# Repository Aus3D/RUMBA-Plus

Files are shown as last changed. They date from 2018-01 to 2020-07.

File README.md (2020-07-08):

# RUMBA+




RUMBA+ is an updated version of the RUMBA 3D Printer control board, originally developed by [RepRapDiscount](http://www.reprapdiscount.com/). 

The RUMBA+ update is designed to address several shortcomings with the original design, and improve on the otherwise solid framework it presents. More information on RUMBA is available on the RepRapWiki page [here](http://reprap.org/wiki/RUMBA).

Some of the key improvements in the RUMBA+ design include:
* Full 12/24V Compatibility (original RUMBA had 16V limit on bed)
* Better, logic-level MOSFETs which generate less heat (can handle higher currents + safer & more reliable)
* Improved power supply circuitry, including:
  * 5V and 12V regulators completely overhauled for higher current + less heat
  * Automatic power-select between USB or 12/24V
* Higher quality screw terminals for power input / heated bed (higher current rating + easier to work with heavy-gauge wire)
* Dozens of smaller changes to improve reliability or performance - refer to the [release page](https://github.com/Aus3D/RUMBA-Plus/releases) for a detailed change history.

RUMBA+ boards are for sale in the [Aus3D shop](http://aus3d.com.au/rumba-plus). Additional documentation is available on the [Aus3D wiki](http://wiki.aus3d.com.au/RUMBA_Plus).

In keeping with the original RUMBA design, RUMBA+ is fully open source.

## Images
### Overview
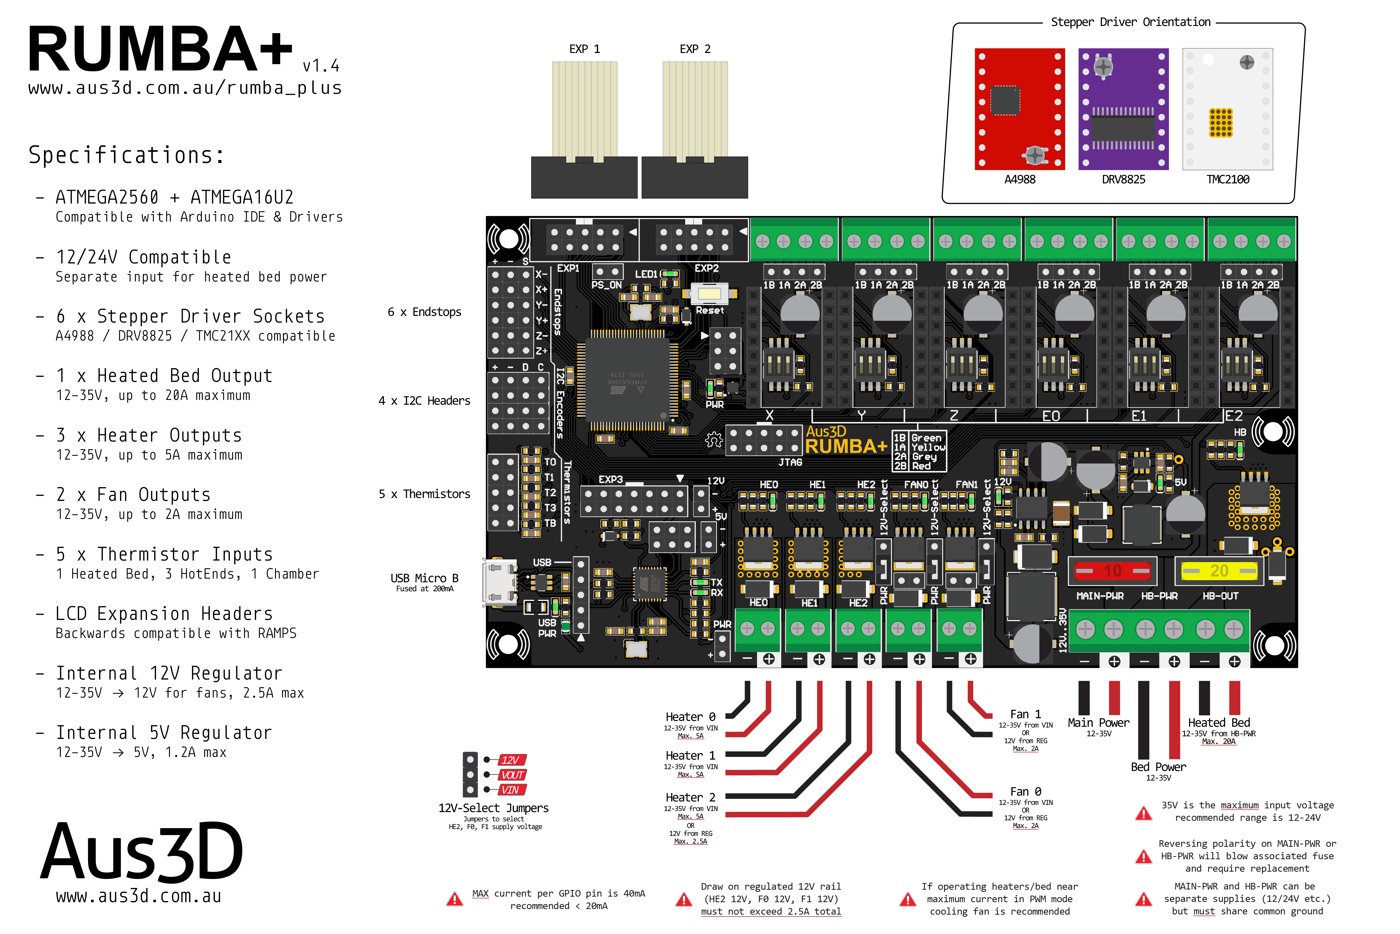
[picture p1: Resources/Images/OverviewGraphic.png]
RUMBA+ Overview

### Photo
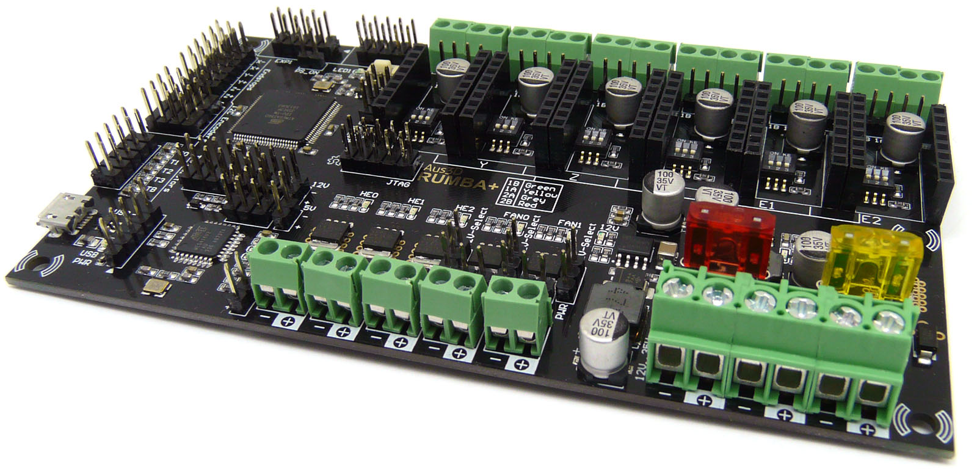
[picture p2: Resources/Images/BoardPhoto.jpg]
RUMBA+ Photo

### Schematic
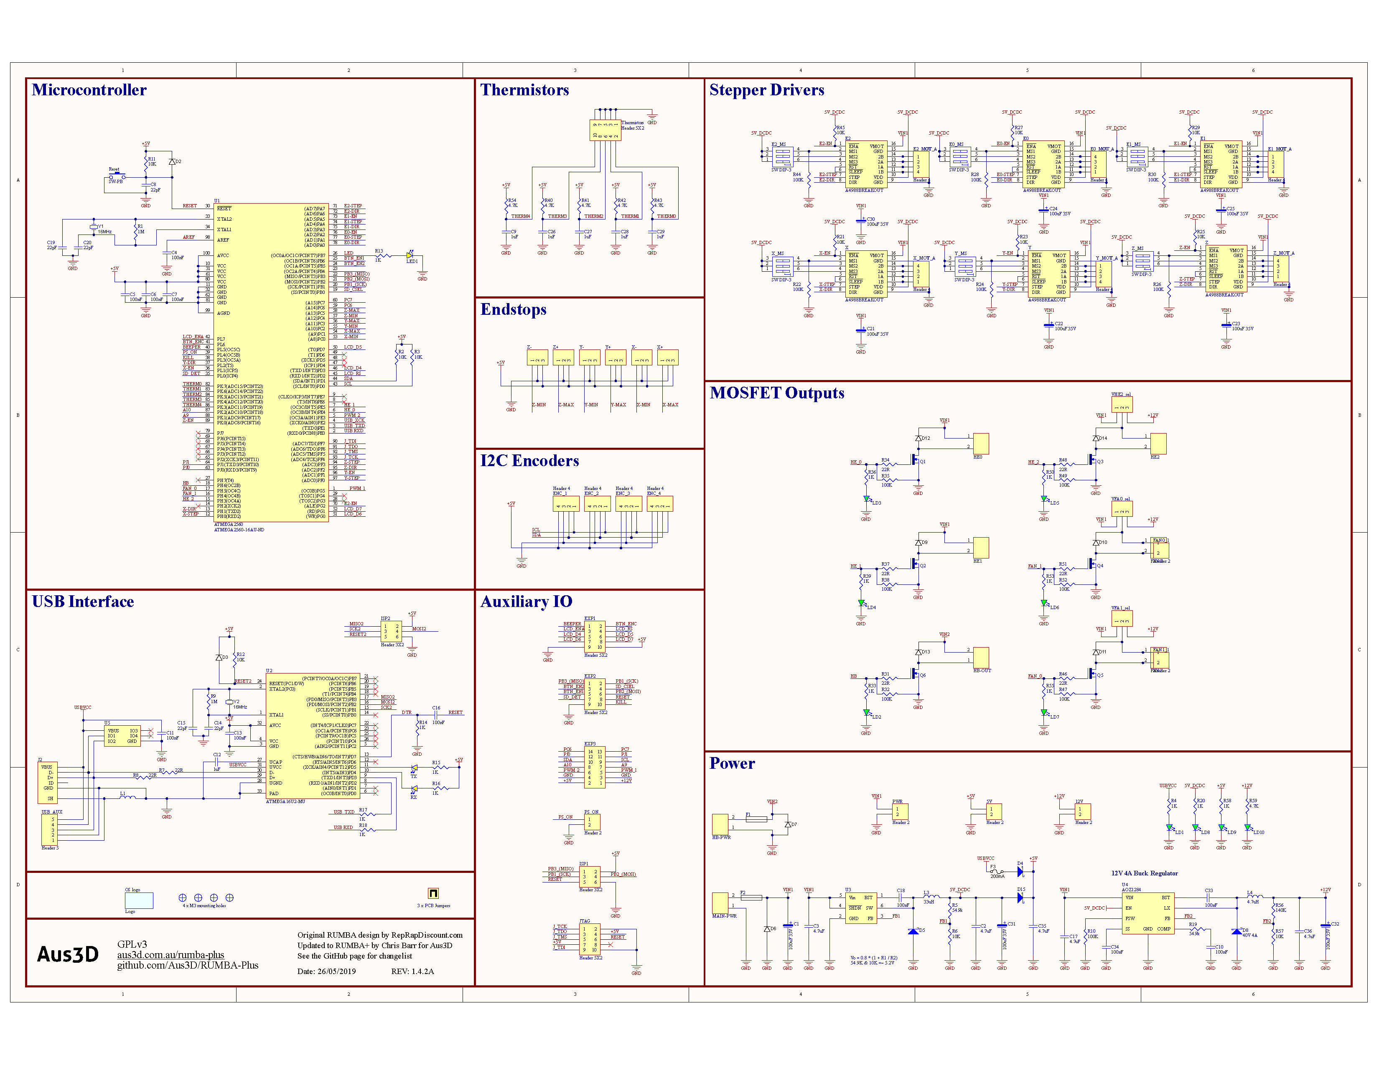
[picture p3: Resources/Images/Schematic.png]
RUMBA+ Schematic

### Pinout
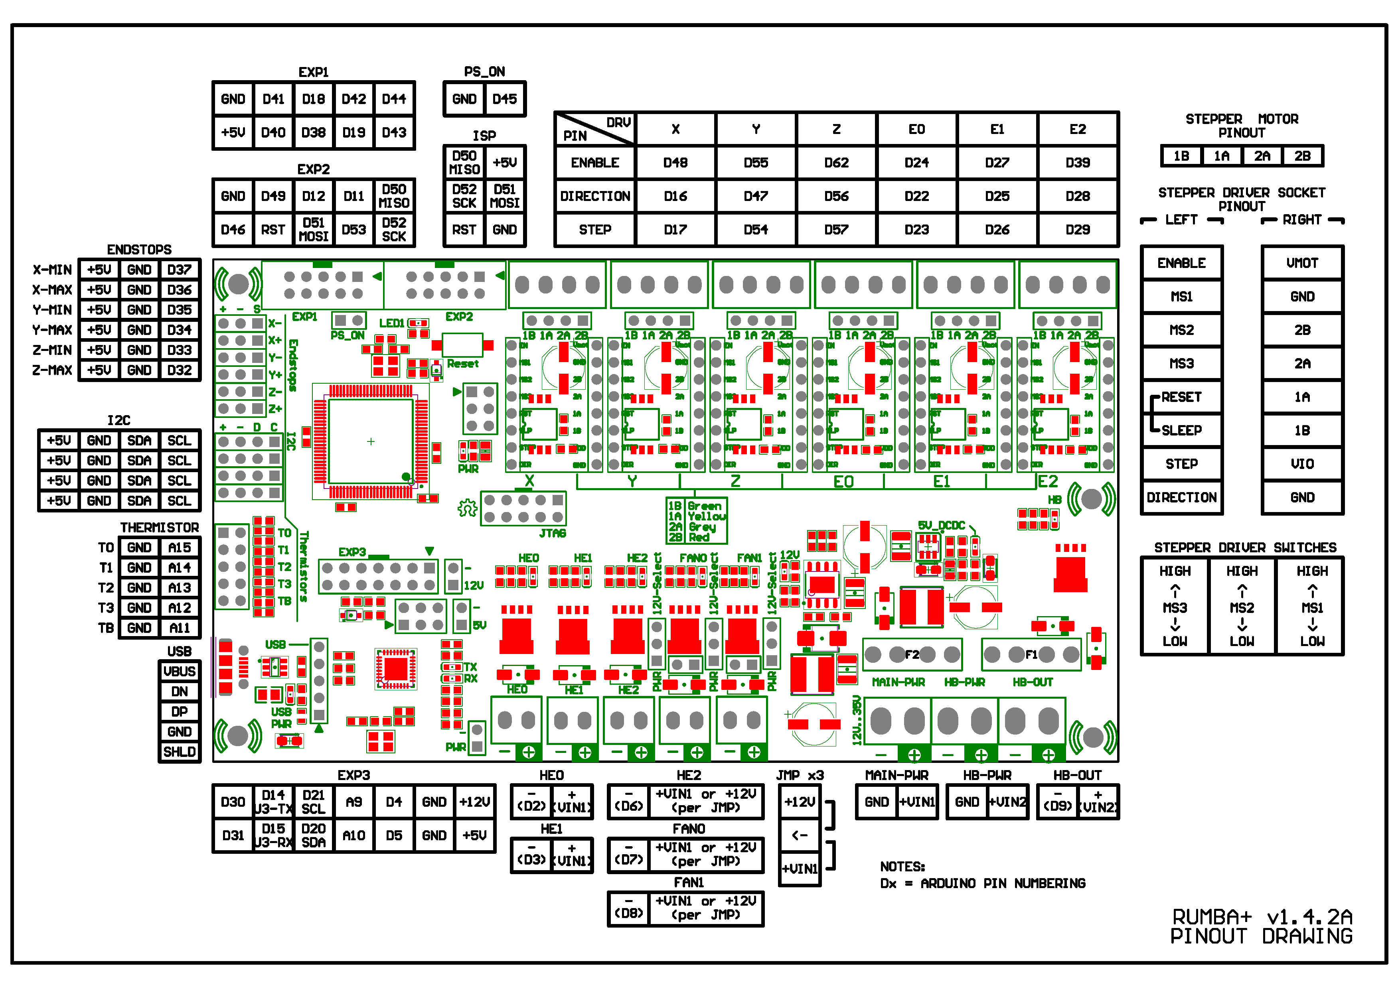
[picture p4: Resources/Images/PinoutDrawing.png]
RUMBA+ Pinout

### Dimensions
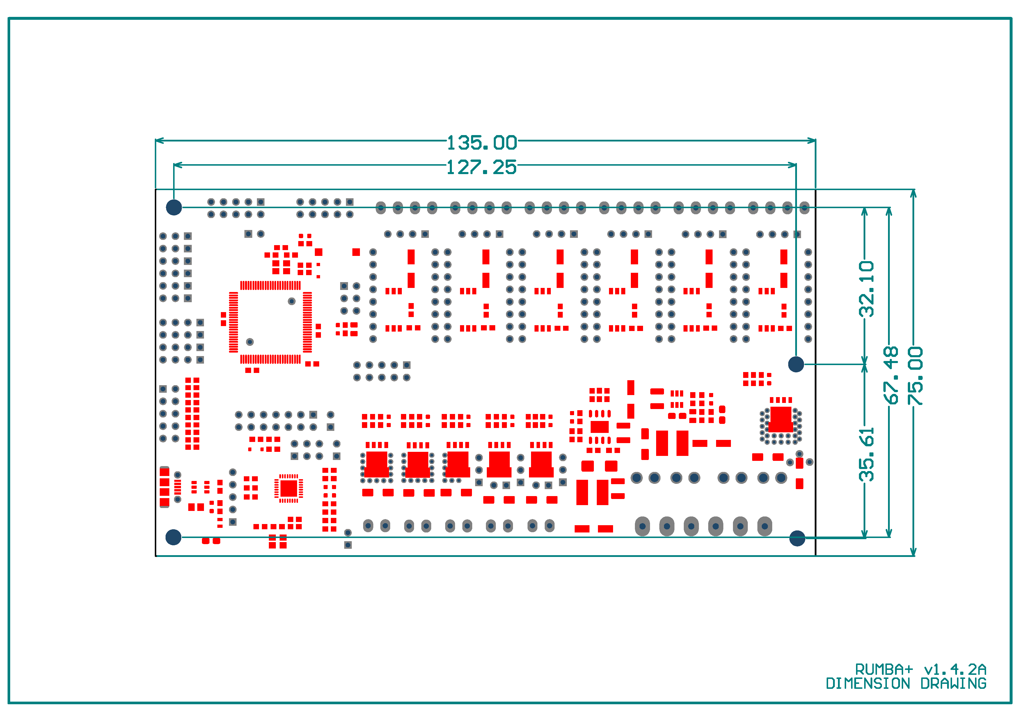
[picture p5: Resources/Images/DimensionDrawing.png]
RUMBA+ Dimensions


## License
RUMBA+ is fully open source, and may be freely modified or changed by anyone, provided they maintain the license it is released under. The design is free to use for any purpose, including commercial uses. RUMBA+ maintains the GPLv2 license of the original RUMBA board. For more information on this license, please see the included license file.

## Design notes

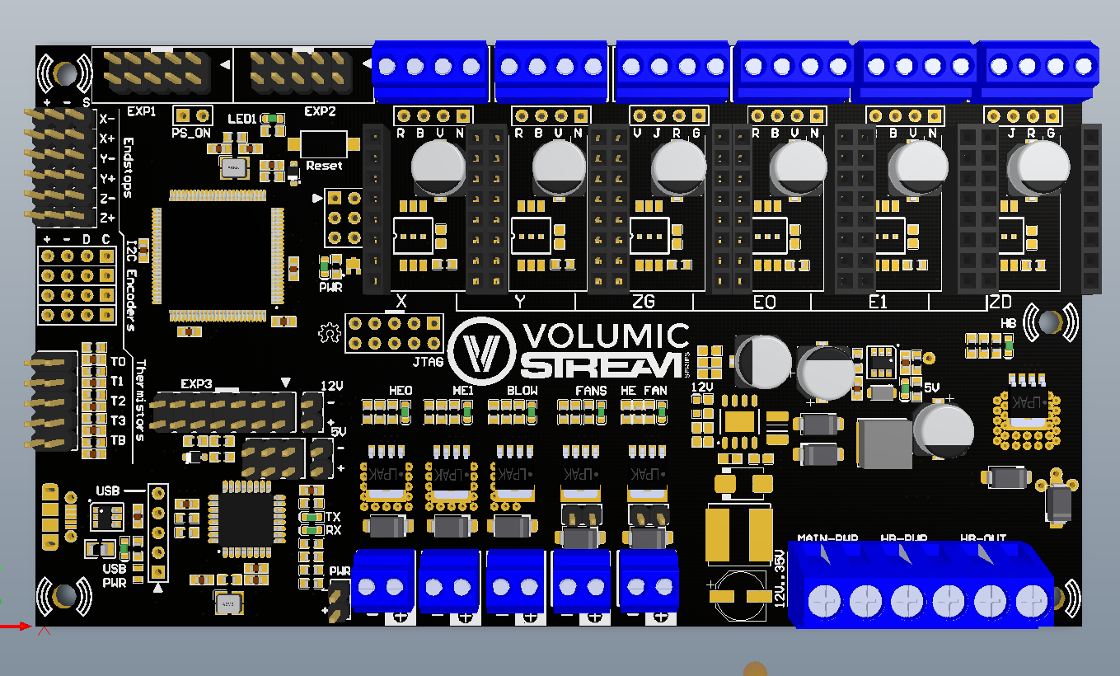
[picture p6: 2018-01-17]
V3D-RUMBA_plus_BoardPreviewTop_1_4_0.png

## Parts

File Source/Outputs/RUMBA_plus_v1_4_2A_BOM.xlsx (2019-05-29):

Designator | Description | Quantity | Note | Manufacturer 1 | Manufacturer Part Number 1 | Supplier 1 | Supplier Part Number 1
JMP | 2.54mm .1" PCB Jumper, Green | 3 | Installed as per drawing, approved sub OK | Sullins (https://octopart-clicks.com/click/altium?sku=S9337-ND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) | QPC02SXGN-RC (https://octopart-clicks.com/click/altium?sku=S9337-ND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) | Digi-Key | S9337-ND (https://octopart-clicks.com/click/altium?sku=S9337-ND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)
C1, C21, C22, C23, C24, C25, C30, C31, C32 | CAP ALUM 100UF 20% 35V SMD | 9 | Approved sub OK | Panasonic (https://octopart-clicks.com/click/altium?sku=PCE5016CT-ND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) | EEEFT1V101AP (https://octopart-clicks.com/click/altium?sku=PCE5016CT-ND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) | Digi-Key | PCE5016CT-ND (https://octopart-clicks.com/click/altium?sku=PCE5016CT-ND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)
C4, C5, C6, C7, C10, C11, C13, C16, C18, C33, C34 | CAP CER 0.1UF 50V X7R 0603 | 11 | Approved sub OK | Yageo (https://octopart-clicks.com/click/altium?sku=311-1344-1-ND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) | CC0603KRX7R9BB104 (https://octopart-clicks.com/click/altium?sku=311-1344-1-ND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) | Digi-Key | 311-1344-1-ND (https://octopart-clicks.com/click/altium?sku=311-1344-1-ND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)
C9, C12, C26, C27, C28, C29 | CAP CER 1UF 16V X7R 0603 | 6 | Approved sub OK | Taiyo Yuden (https://octopart-clicks.com/click/altium?sku=587-1241-1-ND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) | EMK107B7105KA-T (https://octopart-clicks.com/click/altium?sku=587-1241-1-ND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) | Digi-Key | 587-1241-1-ND (https://octopart-clicks.com/click/altium?sku=587-1241-1-ND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)
C2, C35 | CAP CER 4.7UF 10V X7R 0805 | 2 | Approved sub OK | TDK (https://octopart-clicks.com/click/altium?sku=445-14527-1-ND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) | C2012X7R1A475K085AC (https://octopart-clicks.com/click/altium?sku=445-14527-1-ND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) | Digi-Key | 445-14527-1-ND (https://octopart-clicks.com/click/altium?sku=445-14527-1-ND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)
C3, C17, C36 | CAP CER 4.7UF 50V X7R 1210 | 3 | Approved sub OK | KEMET (https://octopart-clicks.com/click/altium?sku=399-6785-1-ND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) | C1210C475K5RACTU (https://octopart-clicks.com/click/altium?sku=399-6785-1-ND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) | Digi-Key | 399-6785-1-ND (https://octopart-clicks.com/click/altium?sku=399-6785-1-ND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)
C8, C14, C15, C19, C20 | CAP CER 22PF 50V X7R 0603 | 5 | Approved sub OK | Kyocera AVX (https://octopart-clicks.com/click/altium?sku=478-6204-1-ND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) | 06035C220JAT2A (https://octopart-clicks.com/click/altium?sku=478-6204-1-ND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) | Digi-Key | 478-6204-1-ND (https://octopart-clicks.com/click/altium?sku=478-6204-1-ND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)
J2 | CONN RCPT USB2.0 MICRO B SMD R/A | 1 | Approved sub OK | Molex (https://octopart-clicks.com/click/altium?sku=WM1399CT-ND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) | 105017-0001 (https://octopart-clicks.com/click/altium?sku=WM1399CT-ND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) | Digi-Key | WM1399CT-ND (https://octopart-clicks.com/click/altium?sku=WM1399CT-ND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)
Y1, Y2 | CRYSTAL 16.0000MHZ 18PF SMD | 2 | Approved sub OK | Epson (https://octopart-clicks.com/click/altium?sku=SER3686CT-ND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) | FA-23816.0000MBC3 (https://octopart-clicks.com/click/altium?sku=SER3686CT-ND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) | Digi-Key | SER3686CT-ND (https://octopart-clicks.com/click/altium?sku=SER3686CT-ND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)
D2, D3 | DIODE GEN PURP 75V 150MA SOD323 | 2 | Approved sub OK | MCC (https://octopart-clicks.com/click/altium?sku=1N4148WXTPMSCT-ND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) | 1N4148WX-TP (https://octopart-clicks.com/click/altium?sku=1N4148WXTPMSCT-ND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) | Digi-Key | 1N4148WXTPMSCT-ND (https://octopart-clicks.com/click/altium?sku=1N4148WXTPMSCT-ND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)
D6, D7, D9, D10, D11, D12, D13, D14 | DIODE GEN PURP 100V 1.5A SMA | 8 | Approved sub OK | Diodes (https://octopart-clicks.com/click/altium?sku=S2BA-FDICT-ND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) | S2BA-13-F (https://octopart-clicks.com/click/altium?sku=S2BA-FDICT-ND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) | Digi-Key | S2BA-FDICT-ND (https://octopart-clicks.com/click/altium?sku=S2BA-FDICT-ND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)
D4, D5, D15 | DIODE SCHOTTKY 40V 2A SOD123F | 3 | Approved sub OK | ON Semiconductor / Fairchild (https://octopart-clicks.com/click/altium?manufacturer=ON%20Semiconductor%20%2F%20Fairchild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) | SS24FL (https://octopart-clicks.com/click/altium?manufacturer=ON%20Semiconductor%20%2F%20Fairchild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) | Digi-Key | SS24FLCT-ND (https://octopart-clicks.com/click/altium?manufacturer=ON%20Semiconductor%20%2F%20Fairchild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)
D8 | DIODE SCHOTTKY 40V 4A DO214AA | 1 | Approved sub OK | General Instruments (https://octopart-clicks.com/click/altium?manufacturer=General%20Instruments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) | SSB44-E3/52T (https://octopart-clicks.com/click/altium?manufacturer=General%20Instruments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) | Digi-Key | SSB44-E3/52TGICT-ND (https://octopart-clicks.com/click/altium?manufacturer=General%20Instruments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)
L1 | FERRITE BEAD 220 OHM 0805 1LN | 1 | Approved sub OK | Murata (https://octopart-clicks.com/click/altium?sku=490-1054-1-ND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) | BLM21PG221SN1D (https://octopart-clicks.com/click/altium?sku=490-1054-1-ND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) | Digi-Key | 490-1054-1-ND (https://octopart-clicks.com/click/altium?sku=490-1054-1-ND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)
L4 | FIXED IND 4.7UH 4.5A 26 MOHM SMD | 1 | Approved sub OK | Bourns (https://octopart-clicks.com/click/altium?sku=SRN6045TA-4R7MCT-ND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) | SRN6045TA-4R7M (https://octopart-clicks.com/click/altium?sku=SRN6045TA-4R7MCT-ND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) | Digi-Key | SRN6045TA-4R7MCT-ND (https://octopart-clicks.com/click/altium?sku=SRN6045TA-4R7MCT-ND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)
L3 | FIXED IND 33UH 1.8A 145 MOHM SMD | 1 | Approved sub OK | Bourns (https://octopart-clicks.com/click/altium?sku=SRN6045TA-330MCT-ND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) | SRN6045TA-330M (https://octopart-clicks.com/click/altium?sku=SRN6045TA-330MCT-ND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) | Digi-Key | SRN6045TA-330MCT-ND (https://octopart-clicks.com/click/altium?sku=SRN6045TA-330MCT-ND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)
F1, F2 | FUSE HOLDER BLADE PCB | 2 | Approved sub OK | Memory Protection Devices (https://octopart-clicks.com/click/altium?sku=BK-6013-ND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) | BK-6013 (https://octopart-clicks.com/click/altium?sku=BK-6013-ND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) | Digi-Key | BK-6013-ND (https://octopart-clicks.com/click/altium?sku=BK-6013-ND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)
5V, 12V, FAN0_1, FAN1_1, PS_ON, PWR | Header, 2-Pin | 6 | Approved sub OK | Generic Header
VFA0_sel, VFA1_sel, VHE2_sel, X-, X+, Y-, Y+, Z-, Z+ | Header, 3-Pin | 9 | Approved sub OK | Generic Header
ISP1, ISP2 | Header, 3-Pin, Dual row | 2 | Approved sub OK | Generic Header
E0_MOT_A, E1_MOT_A, E2_MOT_A, ENC_1, ENC_2, ENC_3, ENC_4, X_MOT_A, Y_MOT_A, Z_MOT_A | Header, 4-Pin | 10 | Approved sub OK | Generic Header
USB_AUX | Header, 5-Pin | 1 | Approved sub OK | Generic Header
EXP1, EXP2, JTAG, Thermistors | Header, 5-Pin, Dual row | 4 | Approved sub OK | Generic Header
EXP3 | Header, 7-Pin, Dual row | 1 | Approved sub OK | Generic Header
E0_0, E0_1, E1_0, E1_1, E2_0, E2_1, X_1, X_2, Y_0, Y_1, Z_0, Z_1 | Header, 8-Pin, Female | 12 | Approved sub OK | Generic Header
U2 | IC MCU 8BIT 16KB FLASH 32VQFN | 1 |  | Microchip (https://octopart-clicks.com/click/altium?sku=ATMEGA16U2-MU-ND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) | ATMEGA16U2-MU (https://octopart-clicks.com/click/altium?sku=ATMEGA16U2-MU-ND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) | Digi-Key | ATMEGA16U2-MU-ND (https://octopart-clicks.com/click/altium?sku=ATMEGA16U2-MU-ND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)
U1 | IC MCU 8BIT 256KB FLASH 100TQFP | 1 |  | Microchip / Atmel (https://octopart-clicks.com/click/altium?manufacturer=Microchip%20%2F%20Atmel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) | ATMEGA2560-16AU (https://octopart-clicks.com/click/altium?manufacturer=Microchip%20%2F%20Atmel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) | Digi-Key | ATMEGA2560-16AU-ND (https://octopart-clicks.com/click/altium?manufacturer=Microchip%20%2F%20Atmel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)
U3 | IC REG BUCK ADJ 1.2A SOT23-6 | 1 |  | Alpha & Omega Semiconductor (https://octopart-clicks.com/click/altium?manufacturer=Alpha%20%26%20Omega%20Semiconductor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) | AOZ1282CI (https://octopart-clicks.com/click/altium?manufacturer=Alpha%20%26%20Omega%20Semiconductor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) | Digi-Key | 785-1613-1-ND (https://octopart-clicks.com/click/altium?manufacturer=Alpha%20%26%20Omega%20Semiconductor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)
U4 | IC REG BUCK ADJ 4A 8SO | 1 |  | Alpha & Omega Semiconductor (https://octopart-clicks.com/click/altium?manufacturer=Alpha%20%26%20Omega%20Semiconductor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) | AOZ1284PI (https://octopart-clicks.com/click/altium?manufacturer=Alpha%20%26%20Omega%20Semiconductor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) | Digi-Key | 785-1689-1-ND (https://octopart-clicks.com/click/altium?manufacturer=Alpha%20%26%20Omega%20Semiconductor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)
LD1, LD2, LD3, LD4, LD5, LD6, LD7, LD8, LD9, LD10 | LED GREEN CLEAR CHIP SMD 0603 | 10 | Approved sub OK | Vishay Lite-On (https://octopart-clicks.com/click/altium?sku=160-1435-2-ND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) | LTST-C190KGKT (https://octopart-clicks.com/click/altium?sku=160-1435-2-ND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) | Digi-Key | 160-1435-2-ND (https://octopart-clicks.com/click/altium?sku=160-1435-2-ND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)
LED1, RX, TX | LED YELLOW CLEAR CHIP SMD 0603 | 3 | Approved sub OK | Vishay Lite-On (https://octopart-clicks.com/click/altium?sku=160-1437-1-ND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) | LTST-C190KSKT (https://octopart-clicks.com/click/altium?sku=160-1437-1-ND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) | Digi-Key | 160-1437-1-ND (https://octopart-clicks.com/click/altium?sku=160-1437-1-ND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)
Q1, Q2, Q3, Q4, Q5 | MOSFET N-CH 40V 33A LFPAK | 5 |  | Nexperia (https://octopart-clicks.com/click/altium?sku=1727-1123-1-ND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) | BUK9Y21-40E,115 (https://octopart-clicks.com/click/altium?sku=1727-1123-1-ND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) | Digi-Key | 1727-1123-1-ND (https://octopart-clicks.com/click/altium?sku=1727-1123-1-ND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)
Q6 | MOSFET N-CH 40V 100A LFPAK | 1 |  | Nexperia (https://octopart-clicks.com/click/altium?sku=1727-1052-1-ND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) | PSMN1R8-40YLC,115 (https://octopart-clicks.com/click/altium?sku=1727-1052-1-ND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) | Digi-Key | 1727-1052-1-ND (https://octopart-clicks.com/click/altium?sku=1727-1052-1-ND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)
F3 | PTC RESET FUSE 9V 200MA 0603 | 1 | Approved sub OK | Bel (https://octopart-clicks.com/click/altium?sku=507-1821-1-ND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) | 0ZCM0020FF2G (https://octopart-clicks.com/click/altium?sku=507-1821-1-ND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) | Digi-Key | 507-1821-1-ND (https://octopart-clicks.com/click/altium?sku=507-1821-1-ND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)
R4, R13, R14, R15, R16, R17, R18, R20, R33, R36, R39, R50, R53, R55, R58 | RES SMD 1K OHM 1% 1/10W 0603 | 15 | Approved sub OK | Yageo (https://octopart-clicks.com/click/altium?sku=311-1.00KHRCT-ND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) | RC0603FR-071KL (https://octopart-clicks.com/click/altium?sku=311-1.00KHRCT-ND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) | Digi-Key | 311-1.00KHRCT-ND (https://octopart-clicks.com/click/altium?sku=311-1.00KHRCT-ND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)
R1, R9 | RES SMD 1M OHM 1% 1/10W 0603 | 2 | Approved sub OK | Yageo (https://octopart-clicks.com/click/altium?sku=311-1.00MHRDKR-ND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) | RC0603FR-071ML (https://octopart-clicks.com/click/altium?sku=311-1.00MHRDKR-ND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) | Digi-Key | 311-1.00MHRDKR-ND (https://octopart-clicks.com/click/altium?sku=311-1.00MHRDKR-ND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)
R40, R41, R42, R43, R54, R59 | RES SMD 4.7K OHM 1% 1/10W 0603 | 6 | Approved sub OK | Yageo (https://octopart-clicks.com/click/altium?sku=311-4.70KHRCT-ND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) | RC0603FR-074K7L (https://octopart-clicks.com/click/altium?sku=311-4.70KHRCT-ND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) | Digi-Key | 311-4.70KHRCT-ND (https://octopart-clicks.com/click/altium?sku=311-4.70KHRCT-ND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)
R2, R3, R6, R11, R12, R21, R23, R25, R27, R29, R45, R57 | RES SMD 10K OHM 1% 1/10W 0603 | 12 | Approved sub OK | Yageo Phycomp (https://octopart-clicks.com/click/altium?sku=311-10.0KHRCT-ND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) | RC0603FR-0710KL (https://octopart-clicks.com/click/altium?sku=311-10.0KHRCT-ND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) | Digi-Key | 311-10.0KHRCT-ND (https://octopart-clicks.com/click/altium?sku=311-10.0KHRCT-ND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)
R7, R8, R31, R34, R37, R46, R48, R51 | RES SMD 22 OHM 1% 1/10W 0603 | 8 | Approved sub OK | Yageo (https://octopart-clicks.com/click/altium?sku=311-22.0HRCT-ND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) | RC0603FR-0722RL (https://octopart-clicks.com/click/altium?sku=311-22.0HRCT-ND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) | Digi-Key | 311-22.0HRCT-ND (https://octopart-clicks.com/click/altium?sku=311-22.0HRCT-ND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)
R5, R19 | RES SMD 54.9K OHM 1% 1/10W 0603 | 2 | Approved sub OK | Yageo (https://octopart-clicks.com/click/altium?sku=311-54.9KHRCT-ND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) | RC0603FR-0754K9L (https://octopart-clicks.com/click/altium?sku=311-54.9KHRCT-ND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) | Digi-Key | 311-54.9KHRCT-ND (https://octopart-clicks.com/click/altium?sku=311-54.9KHRCT-ND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)
R10, R22, R24, R26, R28, R30, R32, R35, R38, R44, R47, R49, R52 | RES SMD 100K OHM 1% 1/10W 0603 | 13 | Approved sub OK | Yageo (https://octopart-clicks.com/click/altium?sku=311-100KHRCT-ND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) | RC0603FR-07100KL (https://octopart-clicks.com/click/altium?sku=311-100KHRCT-ND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) | Digi-Key | 311-100KHRCT-ND (https://octopart-clicks.com/click/altium?sku=311-100KHRCT-ND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)
R56 | RES SMD 140K OHM 1% 1/10W 0603 | 1 | Approved sub OK | Yageo (https://octopart-clicks.com/click/altium?sku=311-140KHRCT-ND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) | RC0603FR-07140KL (https://octopart-clicks.com/click/altium?sku=311-140KHRCT-ND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) | Digi-Key | 311-140KHRCT-ND (https://octopart-clicks.com/click/altium?sku=311-140KHRCT-ND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)
E0_MS, E1_MS, E2_MS, X_MS, Y_MS, Z_MS | SWITCH SLIDE DIP SPST 25MA 24V | 6 | Approved sub OK | Wurth Electronics (https://octopart-clicks.com/click/altium?sku=732-3853-1-ND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) | 416131160803 (https://octopart-clicks.com/click/altium?sku=732-3853-1-ND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) | Digi-Key | 732-3853-1-ND (https://octopart-clicks.com/click/altium?sku=732-3853-1-ND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)
Reset | SWITCH TACTILE SPST-NO 0.05A 12V | 1 | Approved sub OK | APEM (https://octopart-clicks.com/click/altium?sku=679-2396-1-ND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) | MJTP1106SATR (https://octopart-clicks.com/click/altium?sku=679-2396-1-ND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) | Digi-Key | 679-2396-1-ND (https://octopart-clicks.com/click/altium?sku=679-2396-1-ND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)
FAN0, FAN1, HE0, HE1, HE2 | TERM BLK 2POS SIDE ENT 3.5MM PCB | 5 | Approved sub OK | Phoenix Contact (https://octopart-clicks.com/click/altium?sku=277-5719-ND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) | MKDS1/2-3,5 (https://octopart-clicks.com/click/altium?sku=277-5719-ND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) | Digi-Key | 277-5719-ND (https://octopart-clicks.com/click/altium?sku=277-5719-ND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)
HB-OUT, HB-PWR, MAIN-PWR | TERM BLK 2POS SIDE ENTRY 5MM PCB | 3 |  | Phoenix Contact (https://octopart-clicks.com/click/altium?sku=277-6405-ND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) | 1935776 (https://octopart-clicks.com/click/altium?sku=277-6405-ND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) | Digi-Key | 277-6405-ND (https://octopart-clicks.com/click/altium?sku=277-6405-ND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)
E0_MOT, E1_MOT, E2_MOT, X_MOT, Y_MOT, Z_MOT | TERM BLK 4POS SIDE ENT 3.5MM PCB | 6 | Approved sub OK | Phoenix Contact (https://octopart-clicks.com/click/altium?sku=277-5744-ND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) | MKDS1/4-3,5 (https://octopart-clicks.com/click/altium?sku=277-5744-ND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) | Digi-Key | 277-5744-ND (https://octopart-clicks.com/click/altium?sku=277-5744-ND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)
U5 | TVS DIODE 5.25V 17V SOT23-6 | 1 | Approved sub OK | STMicroelectronics (https://octopart-clicks.com/click/altium?sku=497-4492-1-ND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) | USBLC6-4SC6 (https://octopart-clicks.com/click/altium?sku=497-4492-1-ND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) | Digi-Key | 497-4492-1-ND (https://octopart-clicks.com/click/altium?sku=497-4492-1-ND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)

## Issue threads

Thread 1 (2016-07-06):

16u2 DTR Pin mistmatch

chrissbarr, 2016-07-06:
DTR pin from 16u2 to reset ATmega2560 on serial connect doesn't match pinout in official Arduino Mega 2560 16u2 firmware. DTR pin is PB0 (pin 14) instead of PD7 (pin 13).

This means that the board won't automatically reset upon serial connection, making firmware upload or connection through a host program difficult.

Potential Solutions:

1. Modify 16u2 firmware to match different pinout. This seems to be what RRD have done with their RUMBA 16u2 firmware, but this means different firmware from the Arduino Mega which is potentially confusing + requires ongoing maintenance.

2. Change pinout to match Arduino Mega2560. Pins 13 and 14 are adjacent, and can be bridged to achieve same outcome on initial batch of boards.

chrissbarr, 2016-07-27:
Fixed in 1127dff. Initial boards reworked accordingly.

Closed 2016-07-27.

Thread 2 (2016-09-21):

16u2 ICSP header clearance

chrissbarr, 2016-09-21:
Programming the 16u2 is tricky because the 5V header physically interferes with connecting to the ICSP header.

Increasing spacing between ISP2 and 5V headers slightly should fix problem.

Closed 2016-09-21.

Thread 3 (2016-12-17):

BT Extension

evandavey, 2016-12-17:
Can a JYU-MCU module be attached similar to http://reprap.org/wiki/RAMPS_1.4#BT_Extension?

chrissbarr, 2016-12-25:
It should definitely be possible. RUMBA+ has all the same pins that are exposed on RAMPS, and a few extra.

I don't have one of the BT modules to test with, but from the look of things the easiest way would be to use pins on the header EXP3, and wire similar to RAMPS. The 5V and GND pins are there, and then you could use PJ1 / D14 as TxD and PJ0 / D15 as RxD. You'd need the same resistors shown in the RAMPS drawing - I didn't check but I assume those values are correct

I've just added a pinout image to the [main page of the repo](https://github.com/Aus3D/RUMBA-Plus), that should help in finding the pins listed above. Note that the pins above (D14 and D15) correspond to serial port 3 in the Arduino setup, so you'd want to change to that port in Marlin:
```
/**
 * Select which serial port on the board will be used for communication with the host.
 * This allows the connection of wireless adapters (for instance) to non-default port pins.
 * Serial port 0 is always used by the Arduino bootloader regardless of this setting.
 *
 * :[0, 1, 2, 3, 4, 5, 6, 7]
 */
#define SERIAL_PORT 3
```

evandavey, 2016-12-28:
Ok, thanks.  Will post back if successful.

evandavey, 2017-01-04:
No success so far.  I have used serial passthrough code to successfully communicate with the module on a stock Arduino Mega (send AT, get OK).  D14 TXD3 is connected to the RXD of the module (with logic translation through a resistor divider), and D15 RXD3 to the TXD of the module.  Module VCC and GND is connected to the Mega 5V/GND.   But I get nothing re-producing this setup on the Rumba+ with module RXD connected to PJ1 on EXP3 and module TXD connected to PJ0 on EXP3. Module VCC / GND is connected to EXP3 5V/GND.  Thoughts?

chrissbarr, 2017-02-04:
Sorry for the late reply.

It's odd that it isn't working with those two pins - they should be exactly the same pins as on the Arduino Mega. I've been double-checking the pinout and I can't see a problem there, but I might be missing something.

Would it be possible to try a different UART? Maybe D18 (TXD1) and D19 (RXD1), which are on the EXP1 header. I didn't suggest these as they would interfere if you're running an LCD, but maybe it's worth testing with them just to see if it's the same result?

Closed 2020-05-27.

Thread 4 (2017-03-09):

Using wago connector of serie 742

bastien-roucaries, 2017-03-09:
It will be nice if pcb could use this kind of terminal

Better amp handling. No more problem with wire (cage clamp is safe) and fuse

 http://www.wagoproducts.com/printed-circuit/series-742/wago-742-111/

Closed 2020-05-27.

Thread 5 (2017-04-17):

USB connectivity

axjurado, 2017-04-17:
Happy to see someone updating this board. I am on my 3rd rumba and have to change them because of the USB connectivity issues. Is this being addressed on this board?

Closed 2017-05-03.

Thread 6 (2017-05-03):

Display connector picture update

axjurado, 2017-05-03:
I just installe dthe new board, and noticed the picture on the display connectors have an issue: the mark that shows the tab on the connector is on the wrong side. Took a few minutes to realize that was the issue. Thanks

Closed 2020-04-26.

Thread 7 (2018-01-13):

How many amps the mosfet for the bed can handle?

valerie16901, 2018-01-13:
I am worried that my bed, which is 300x300 12v, can be drawing to much amperage from the bed mosfet, I am currently measuring about 21 amps, should I get an external mosfet instead?

chrissbarr, 2018-01-14:
Hi @valerie16901!

The bed MOSFET itself should be able to handle 21A without any issue. It will generate a bit of heat, but still less heat than the MOSFETs on a regular RAMPS board would with a 200x200mm 12V bed - so not a dangerous amount. Even without active cooling (i.e., no electronics fan) 21A should be okay - if you want to be doubly safe, a fan blowing over the board should keep the MOSFET's temperature well under control.

The weak link in this setup is the screw terminals on the RUMBA+ board - they're only rated to 15A, and while that rating is likely on the conservative side, that's where you might run into trouble.

If you're comfortable making a modification to the board, I would suggest de-soldering the heated bed screw terminals (both in and out), and soldering your wires directly to the board instead. That will allow you to run 21A without problems.

If that's not an option, I'd suggest making sure that your heated bed wiring is firmly gripped by the screw terminals, and ensuring that there's no room for the wires to work their way loose. If you can, fix the wires in place near the board with a cable tie, so that no movement of the wires will move the connection inside the screw terminals. A fan, with some air blowing over the screw terminals, would also help a little here.

Without the modifications, I'd also suggest limiting the maximum power delivered to the heated bed - depending on how much power you need to heat it up and how quickly you want it to do so, this might not be an attractive option, but I'd suggest exploring it and seeing if it's workable. In Marlin, the option you're after is `#define MAX_BED_POWER`, which, if set to something less than `255`, should limit the average power being delivered to the bed (and the average current through the screw terminals). The further you reduce it the safer you should be, but then the slower the bed will heat up. If you're running this option, it will put a little more stress on the MOSFET - so I'd definitely suggest running a cooling fan in this case.

The only other thing to watch out for is that the heated bed fuse we supply with these boards is rated to 20A, and might blow running your 21A load - you may have already replaced this, or the included fuse might have enough wiggle-room to run 21A for short periods, but it's something that could blow at some point. A 25A fuse should be easy enough to come by, and as they're common automotive fuses, they're usually not too expensive either - you'd be looking for a mini blade fuse.

The other option, and this will depend on your heated bed and the rest of your setup, might be to swap to 24V. If your heated bed allows 12/24V input, then swapping to 24V input would halve your current draw - making it much safer to use the onboard screw terminals. Most standard stepper motors + drivers shouldn't have an issue with the change and often work better with higher voltages, and RUMBA's onboard 12V regulator would still let you run 2-3 12V fans if needed. Depending on your hotend heater cartridge, you might be able to run it from the 12V regulator too - if it's a 25W unit that should be okay, if it's a 40W unit I'd probably advise against it.

If the bed is fixed at 12V, that's probably not an option you want to explore - I just thought I'd put it out there.

So, my suggestions would be:

- Solution A: Remove Screw Terminals
   - Allows maximum current to heat bed as quickly as possible
   - Safest overall solution, also prevents cables from coming loose over time
- Solution B: Reduce Strain on Screw Terminals
   - Limit bed power in firmware to reduce stress on screw terminals
   - Ensure wiring is as tightly gripped as possible and cannot work loose
   - Have a fan blowing air past the screw terminals (or some airflow over whole board)
- Solution C: Swap to 24V
   - Requires no modification to board, no limiting of bed current
   - Potentially allows improved motor performance (depends on driver, motor and configuration)
   - Requires investment in new PSU, possibly heater cartridge, possibly bed

If none of these is workable, your idea to swap to an external MOSFET board might be a good one. You probably won't find a board with a better MOSFET, but they should have heavier-duty screw terminals that will give you the needed headroom.

Let me know if you need any more information, and I'll see what I can do!

valerie16901, 2018-01-14:
Thank you very much for all that information.

I will look at the options, probably I can get a 24v power supply only for the bed, since the rest of my components are rated 12v.

chrissbarr, 2018-01-14:
No worries at all, happy to help!

That sounds like a solid plan. You can definitely use a separate power supply for the bed (something I didn't consider), so provided the bed can support 24V that sounds like a good option.

Let me know if you have any more questions!

wizhippo, 2018-04-09:
@chrissbarr Just out of curiosity according to the data sheet of the PSMN1R8-40YLC and the Safe operating chart I see that at 12 volts it should only be about 8amps.  Am I reading the chart wrong or missing some kind of factor due to the heat dissipation of the board.  I'm sure you are right but I'm just trying to understand the datasheet a bit better.

chrissbarr, 2018-04-10:
@wizhippo No worries at all, happy to help. Safe Operating Charts are always a little misleading at first glance IMO, as you have to really think about what they're showing. Note that the voltage is the drain-source voltage, i.e. the voltage across the MOSFET, and not the supply voltage that you're using (12V/24V etc).

Using the MOSFET as a low-side switch for something like a heated bed, ideally most of the 12V is across the bed, with only a small amount across the MOSFET - it's that small amount we need to consider in the SOA chart.

Assuming the MOSFET is operating in saturation mode (fully on), the drain-source voltage is given by the MOSFET's on-state resistance (RDSon), which is ~ 2mΩ using 5V logic (rating on page 1 or from Fig. 7) and the current flowing through the MOSFET. From Ohm's Law, V=IR, the drain-source voltage at say 15A will be V = 15 x 0.002, or about 0.03V. From the SOA chart, at 0.03V we're in safe territory - not even enough of a voltage drop that it's worth charting, and our likely limit is either given by the total power dissipation, or the total current capability of the MOSFET.

If you're PWMing the MOSFET, you'll change the equation from being primarily conduction losses to primarily switching losses - which take a little more work to calculate. That said, the above shows that we really have an order of magnitude headroom with the MOSFET in this configuration, so even there you won't run into any trouble.

I've tested these MOSFETs as hard as I can on these boards, and I always run into trouble with the screw terminals before anything else - usually around 25A or so they'll be damaged, though I do note they're only rated for 15A (we're looking at improving them on future boards).

If I remove the screw terminals, solder heavy-gauge wire directly to the RUMBA+ board, then there are sections of the PCB itself that are heat-damaged before the MOSFET becomes dangerously hot or becomes damaged. From memory, this happens above 30A or so - it's possible that range could be extended with active cooling.

I've never run into the actual limits of the MOSFET itself. Provided you don't exceed 24V, it shouldn't be possible to physically draw enough current through the board to damage the MOSFET, without first damaging the board or connectors themselves.

I hope that answers your question! Let me know if not, or if there's anything else I can do for you.

chrissbarr, 2018-04-10:
@wizhippo No worries at all, it's a mistake I've made before too so I thought that was probably where the mix-up was.

Anusuya8, 2020-09-25:
Shall I use 24A MOSFET instead of 220A MOSFET for Heat Bed.

chrissbarr, 2020-09-25:
Hi @Anusuya8!

You'd need to provide more information to figure this out. Is there a part number, datasheet or link for the MOSFET you want to use?

Anusuya8, 2020-09-25:
We are going to use the MK2B Heat bed in the SKR V1.4 board. In SKR V1.4 board WSK220N04 MOSFET is driving the Heat bed, whose Ids current rating is 220A Since the current of the (MK2B) heat bed is 20A shall I use IRLR8726TRPBF this MOSFET.

Anusuya8, 2020-09-27:
Hi @chrissbarr <https://github.com/chrissbarr>
We are going to use the MK2B Heat bed in the SKR V1.4 board. In SKR V1.4
board WSK220N04 MOSFET is driving the Heat bed, whose Ids current rating is
220A Since the current of the (MK2B) heat bed is 20A shall I use
IRLR8726TRPBF MOSFET.

Thanks & Regards,
*Ms. Anusuya*
Hardware Engineer

Mob: +91-9962328695

*Embdes Engineering Solutions Pvt. Ltd.,*

No. 567, Mudichur Road, 2nd Floor, SHA Complex,

Lakshmipuram, West Tambaram,

Chennai - 600 045 *|* Tamilnadu *|* India

*GoogleMap*
<https://www.google.com/maps/place/SHA+Complex/@12.925041,80.1009066,15z/data=!4m5!3m4!1s0x0:0x67f5512ade0553c6!8m2!3d12.925041!4d80.1009066>

*www.e2-s.com* <https://e2-s.com/>

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

Closed 2020-05-27.

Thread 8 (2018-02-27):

[Request] New main power connectors

Blaster1920, 2018-02-27:
Hi,
I'm going to make some of this boards, but I actually disagree with this choice for the Bed and PSU connectors. Instead i found very reliable the Duet's ones, with this model number: TJ952-00.
Do you think that could be possible to modify the board in order to use these?
Thanks you for doing the hard work here providing us a very good board!

chrissbarr, 2018-02-28:
Hi @Blaster1920,

Thanks for your kind words!

You're welcome to make a change to the power connectors, or to change the board however you'd like. I'm open to swapping the connectors on the boards we manufacture if there's a good reason for doing so - but I think swapping to the part you suggest might be tricky.

I wasn't able to find a datasheet, but from what I can see the TJ952 are 7.62mm pin spacing, whereas the RUMBA+ board currently has spacing for 5mm screw terminals on the power / heated bed connectors. So swapping to the TJ952 would take up more space width-wise, and we'd either have to make the board wider, or remove something else to make some room. We're trying to keep the layout and dimensions as compatible with the original RUMBA boards as possible, and if we had to make the board bigger that might interfere with that (and obviously we're not keen on removing anything).

The screw terminals we use are meant to be a good mix of size, price and reliability - but there are some other drop-in parts you can explore. Pheonix Contact make some nice [5mm pitch screw terminals that can handle down to 12AWG and carry 20A](https://www.digikey.com/product-detail/en/phoenix-contact/1935776/277-6405-ND/2513905) - we don't use them because they're a bit taller and take up more depth on the board (so they cover up some of the silkscreen labelling), but they are a little easier to use and will handle thicker wiring.

If you really want to use the TJ952, one possible option might be to combine the main power and bed power inputs into a single terminal, so that there would only be two connectors instead of three. I'm not overly keen on doing that with our boards, as we like the flexibility of the separate connectors - but if you're looking to make changes yourself, perhaps that's something to consider.

Blaster1920, 2018-02-28:
Thanks for your reply.
I think that I will modify a little the PCB to remove the hole behind the connectors so I can move there the labels and then use my connector. I'll upload the files if you would like to give them a look.

Blaster1920, 2018-02-28:
I would also like to use thicker copper, how much micron do you suggest?

chrissbarr, 2018-07-16:
Hi @Blaster1920,

Just an update on this. We've updated the screw terminals a little in our latest v1.4 revision. There's still no easy way to fit the connectors you suggested, but there is now room to fit Phoenix Contact 1935776 - which suit up to 10AWG wire and 20A of current. We're using these connectors on new boards that are shipping now.

As for copper thickness - it depends on what your goal is. The default 1 oz copper is sufficient for running a 20A heated bed. If you need more than that, then you'll need to:

- Upgrade the connectors as you planned, to something that can carry the current you're after
- Use a higher-current fuse, or fuse the bed externally and jumper the fuse
- Cool the bed MOSFET, either with a heatsink, fan, or both, depending on how much current you plan to put through it.

You'll need to figure those things out before there's any value in using thicker copper. If you sort those out, then it could be worth stepping up to 2 oz copper.

Closed 2020-05-27.

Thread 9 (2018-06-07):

[Question] AUX1 access

DotBreno, 2018-06-07:
First of all, I love how you replaced the PTC fuses with blade ones. I was just about to do something like that myself. Thanks so much.

My question is about the access to RX0 and TX0 pins, the ones that are labeled as AUX1 on RAMPS 1.4. I noticed you wired the pins RXD0 and TXD0 to USB. Are those the same pins I should use?
I want to do something like [this](https://ae01.alicdn.com/kf/HTB1GWfBSpXXXXcRXVXXq6xXFXXXc.jpg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)
Where it says "MKS TFT". That's the connector I want to add. I just dont know which ports RX and TX should I use in your project. Can you help me?

Also, sorry for the bad english and thanks again for the project.

chrissbarr, 2020-05-27:
Hi @DotBreno,

I have completely missed this question for 2 years now - my sincere apologies on that. I hope that you figured out a working solution to get the MKS TFT running the way you wanted.

For future reference for anyone else that is trying to do something similar, I recommend using the UART3 pins on the EXP3 header. The EXP3 pinout is as follows:

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

So pins PJ1 (TX3) and PJ0 (RX3) would connect to the MKS TFT serial.

Closed 2020-05-27.

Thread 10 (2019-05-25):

BOM incorrect part numbers

chrissbarr, 2019-05-25:
BOM for v1.4 has a few components with incorrect part numbers. These have been corrected during assembly but need to be folded back into the BOM (and Altium schematic too probably).

Incorrect parts are:
- C10
- R19
- R5
- R56

chrissbarr, 2019-05-25:
Fixed in 0091e210f74c37d4cd9082801ec544d5bc2ef77d

Closed 2019-05-25.

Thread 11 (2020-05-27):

TX/RX Pins on Exp 3 - QUESTION

axjurado, 2020-05-27:
Been trying to connect the Wifi Backpack from Panucatt to the board. I can connect but seems like I cannot make it communicate with he rumba+.

The documentation says pin 11 and 12 should be tx rx. However, read here in other question that is pin 13 and 14. Not sure which one should use.

Also, not sure what changes is marlin are needed to make this work.

Appreciate your help. Thanks

chrissbarr, 2020-05-27:
Hi @axjurado,

UART3 is on pins PJ0 (RX) and PJ1 (TX). These are pin 11 and 12, from the below part of the schematic:

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

Here's a top-down view of the EXP3 connector pinout:

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

Hope that clears things up. If you're still stuck let me know and we'll figure it out.

axjurado, 2020-05-27:
thanks chris, i think i  got that part right.

what i don't know is what to change in the firmware to make it work. Tried the serial_port2 3 but didn't work, nor turning on the bluetooth. Any ideas?

BTW Rumba+ is really solid, and want to update it to the rumba32, any idea when will be in stock ?

Thanks for your prompt response and help!

chrissbarr, 2020-05-27:
Hmm, I'm not overly familiar with the WiFi Backpack module, so I'm working through this from reading the wiring info here:

http://panucattdevices.freshdesk.com/support/solutions/articles/1000277389-wiring-guide-wifi-backpacks

I'd check to make sure that RX and TX are connected around the right way (Backpack TX to RUMBA+ RX, and vice-versa).

Your Marlin configuration sounds correct - `#define SERIAL_PORT_2 3` should enable the correct port.

I see in the backpack docs [here](http://panucattdevices.freshdesk.com/support/solutions/articles/1000277681-connecting-to-wifi) that there's a mention of configuring the serial baudrate - you'll want to check that this setting matches your Marlin configuration.

I d not believe that it's necessary to enable Bluetooth in Marlin - as long as the correct port is enabled, that should be the only thing necessary.

Glad to hear you're happy with the RUMBA+ design! I've got a batch of an updated version of RUMBA32 in the works at the moment, if all goes well they should be available in 5-6 weeks.

Let me know if you're still stuck and we'll dig further.

axjurado, 2020-05-27:
Thanks Chris, again.

The Panucatt tech support replied to use #define SERIAL_PORT2 -1, but i thought that 3 was the right number. Does that make sense? I'm not well versed in Marlin to be honest.

Great to hear that the rumba32 will be available soon. Thanks again!

Augusto

chrissbarr, 2020-05-27:
No worries Augusto!

I'm fairly sure that `-1` does not map to a serial port on RUMBA+ and would just be the same as having PORT2 disabled.

There are 4 serial interfaces on the microcontroller in RUMBA+. Here's my understanding of where they go:

UART0  - UART to the 16u2 USB Interface (so this is the USB serial port)
UART1  - maps to pins in EXP1 header
UART2  - unused, maps to pins used for stepper drivers
UART3  - maps to pins in EXP3 header

If you were not going to use USB, you could have port 2 disabled (`SERIAL_PORT_2 -1`) and set port 1 to use UART3 (`SERIAL_PORT 0`). Perhaps the Panucatt support were trying to suggest something like this?

axjurado, 2020-05-27:
Doing SERIAL_PORT_2 3 worked. The -1 wouldn't compile.

My issue with connecting looks like was the baur rate on the wifi backpack.Now it communicates and is working fine.

Thanks for your help! and look forward to the rumba32 to be available!

Closed 2020-05-27.

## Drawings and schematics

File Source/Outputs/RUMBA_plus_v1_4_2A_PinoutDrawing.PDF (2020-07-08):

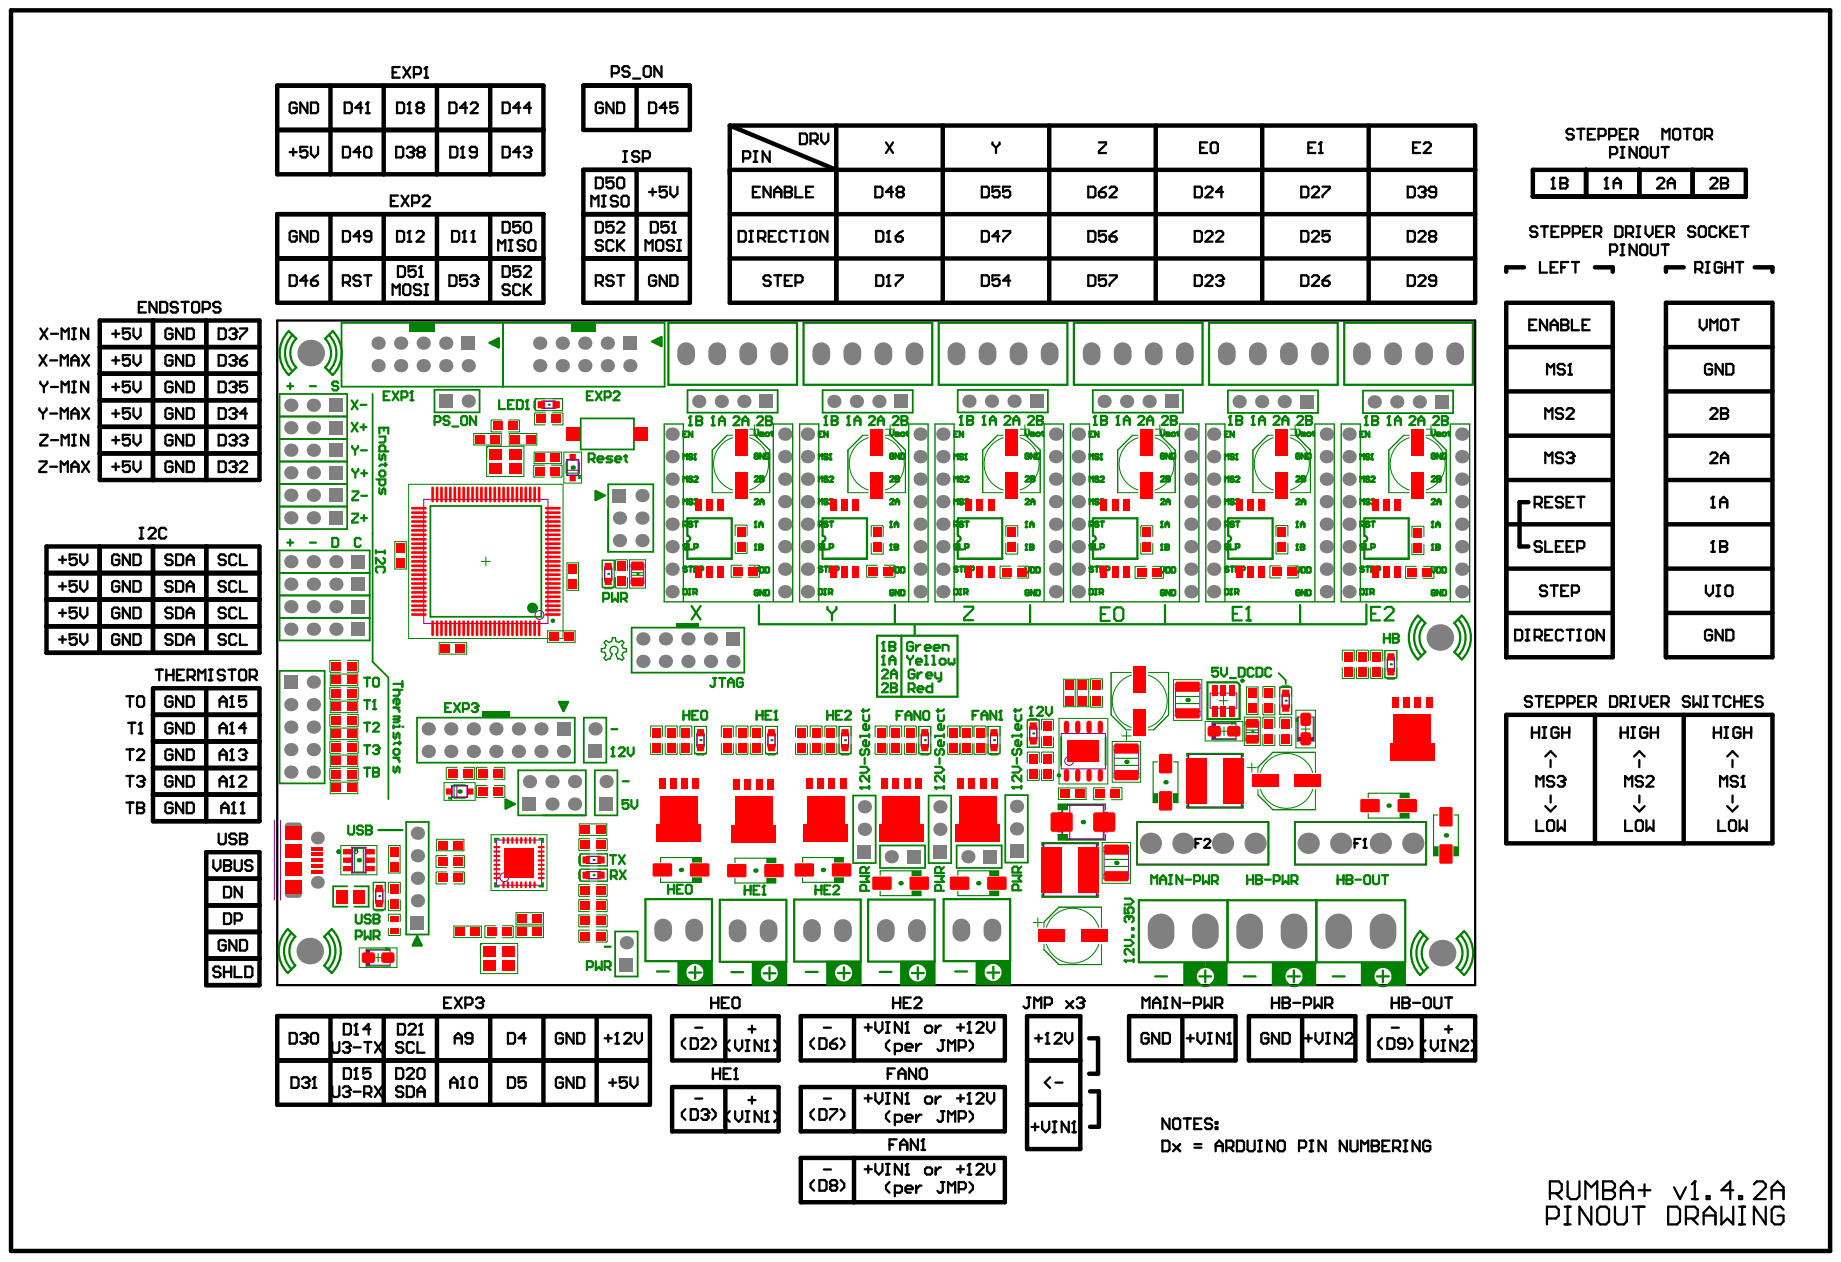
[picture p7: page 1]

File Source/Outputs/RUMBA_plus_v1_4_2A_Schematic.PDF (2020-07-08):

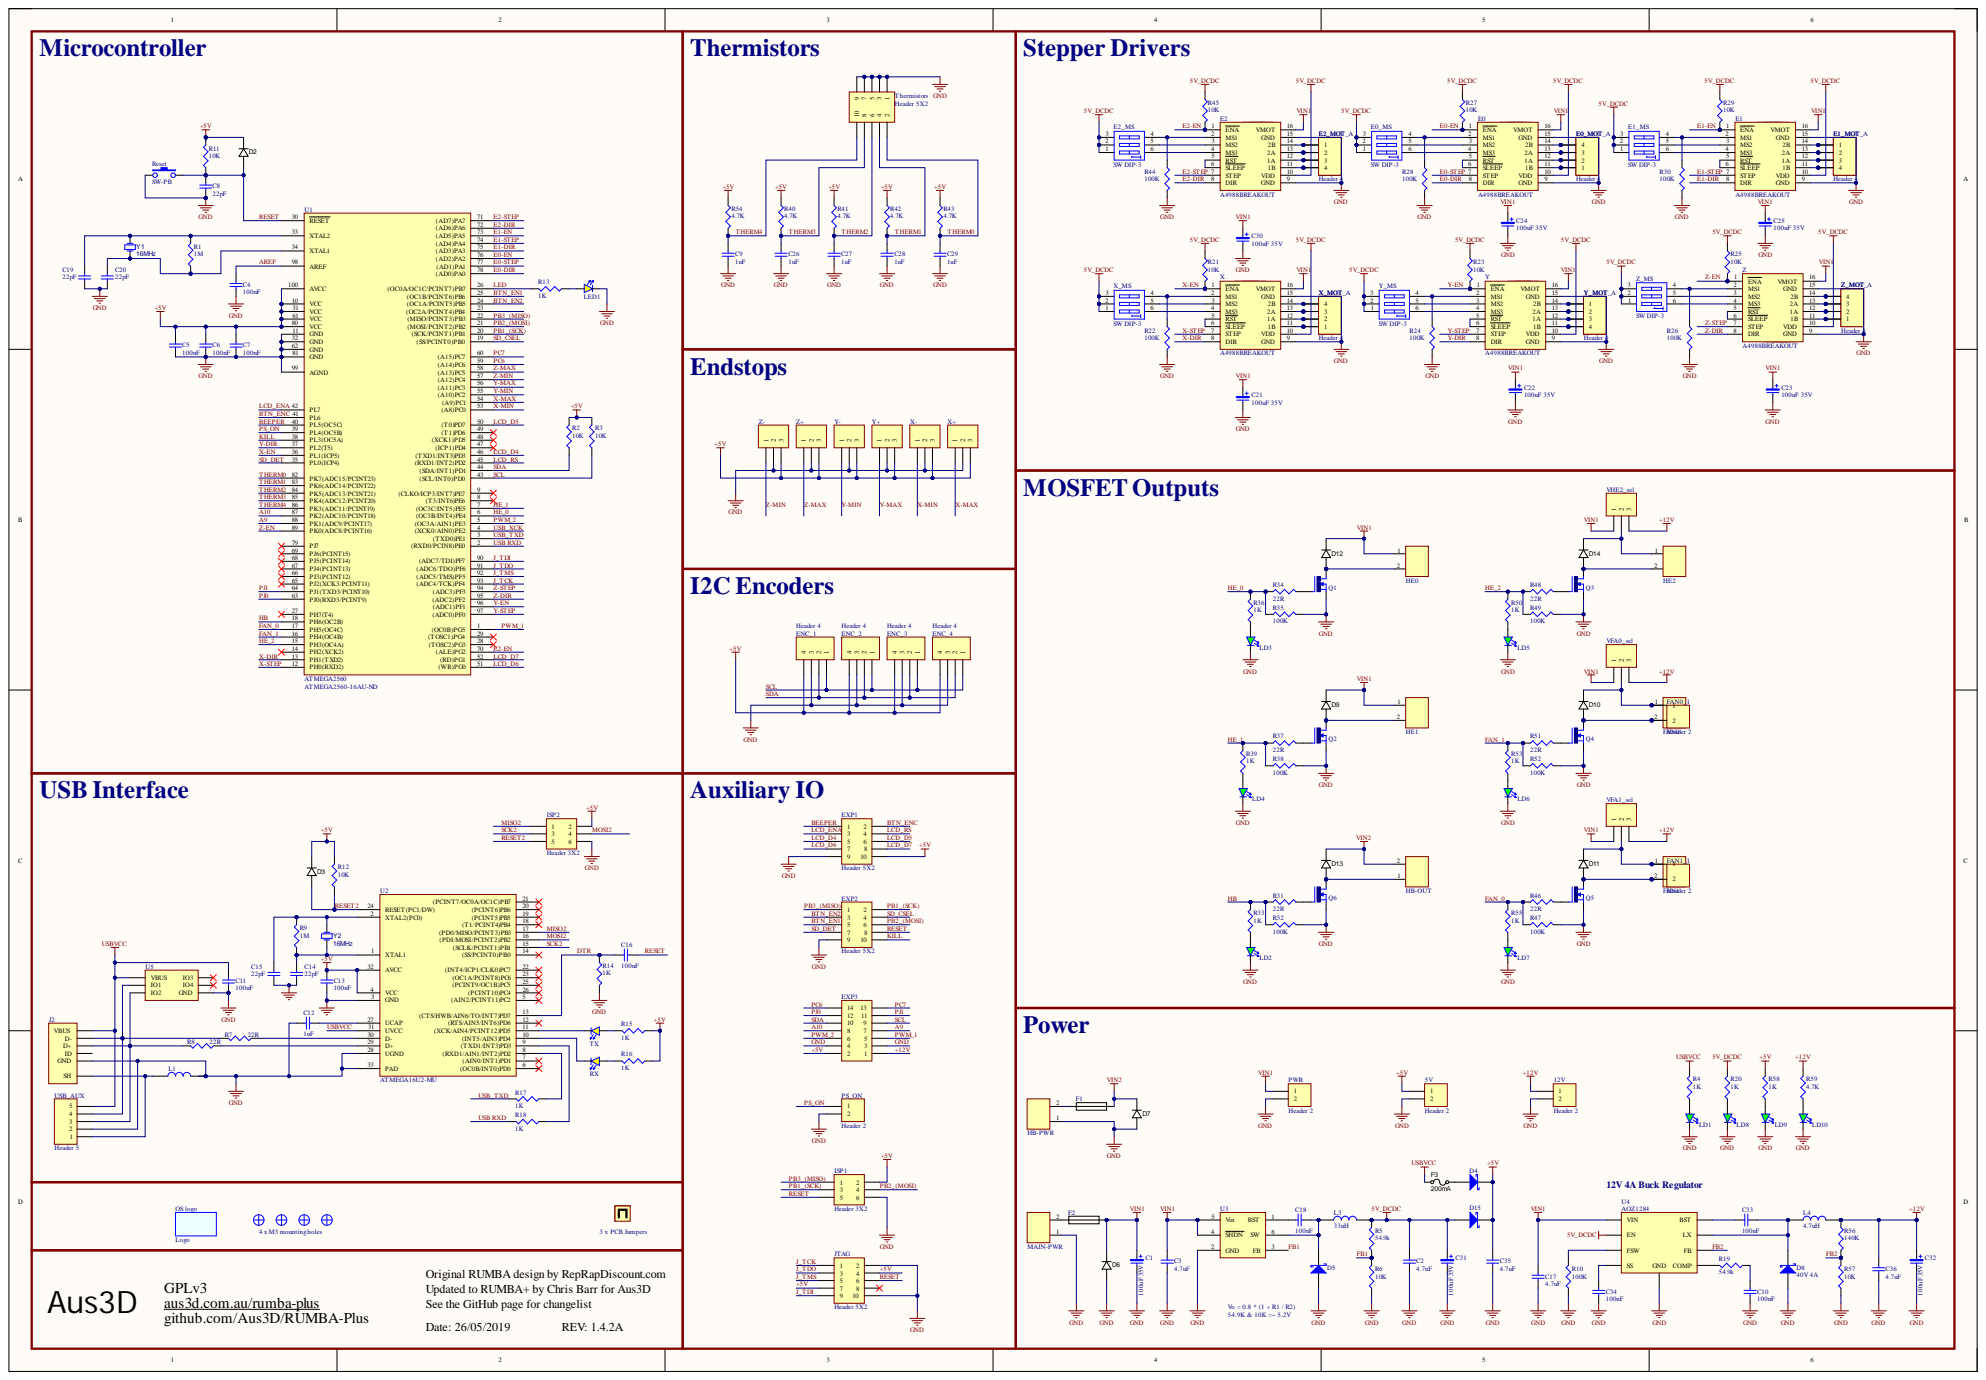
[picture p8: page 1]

ub page for chan
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

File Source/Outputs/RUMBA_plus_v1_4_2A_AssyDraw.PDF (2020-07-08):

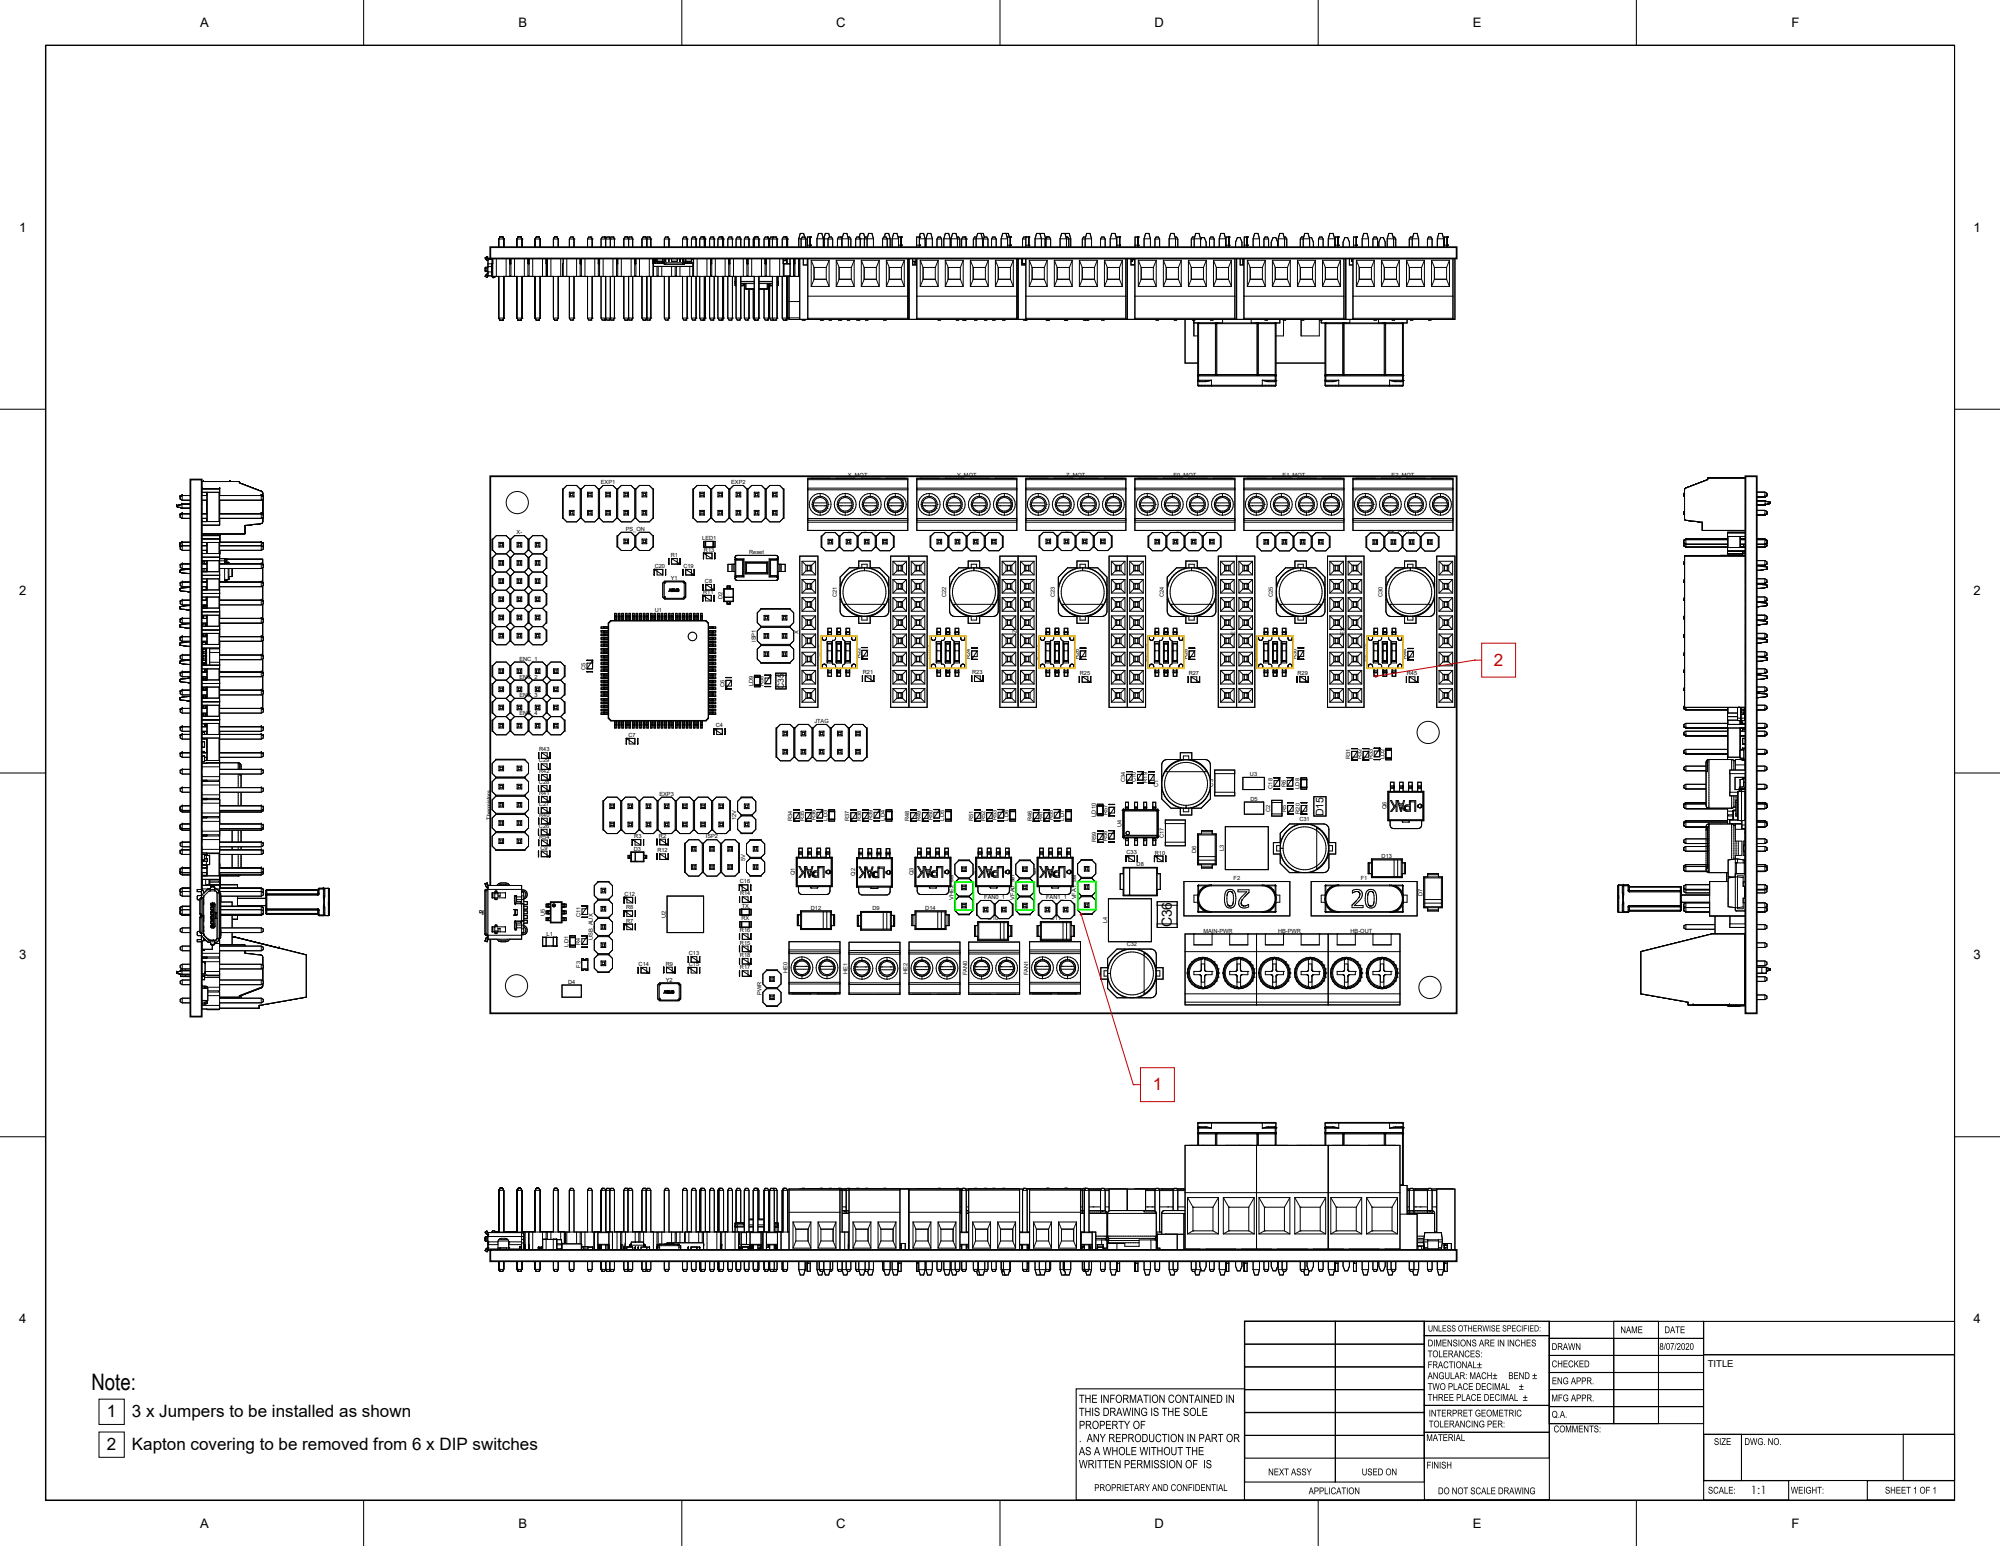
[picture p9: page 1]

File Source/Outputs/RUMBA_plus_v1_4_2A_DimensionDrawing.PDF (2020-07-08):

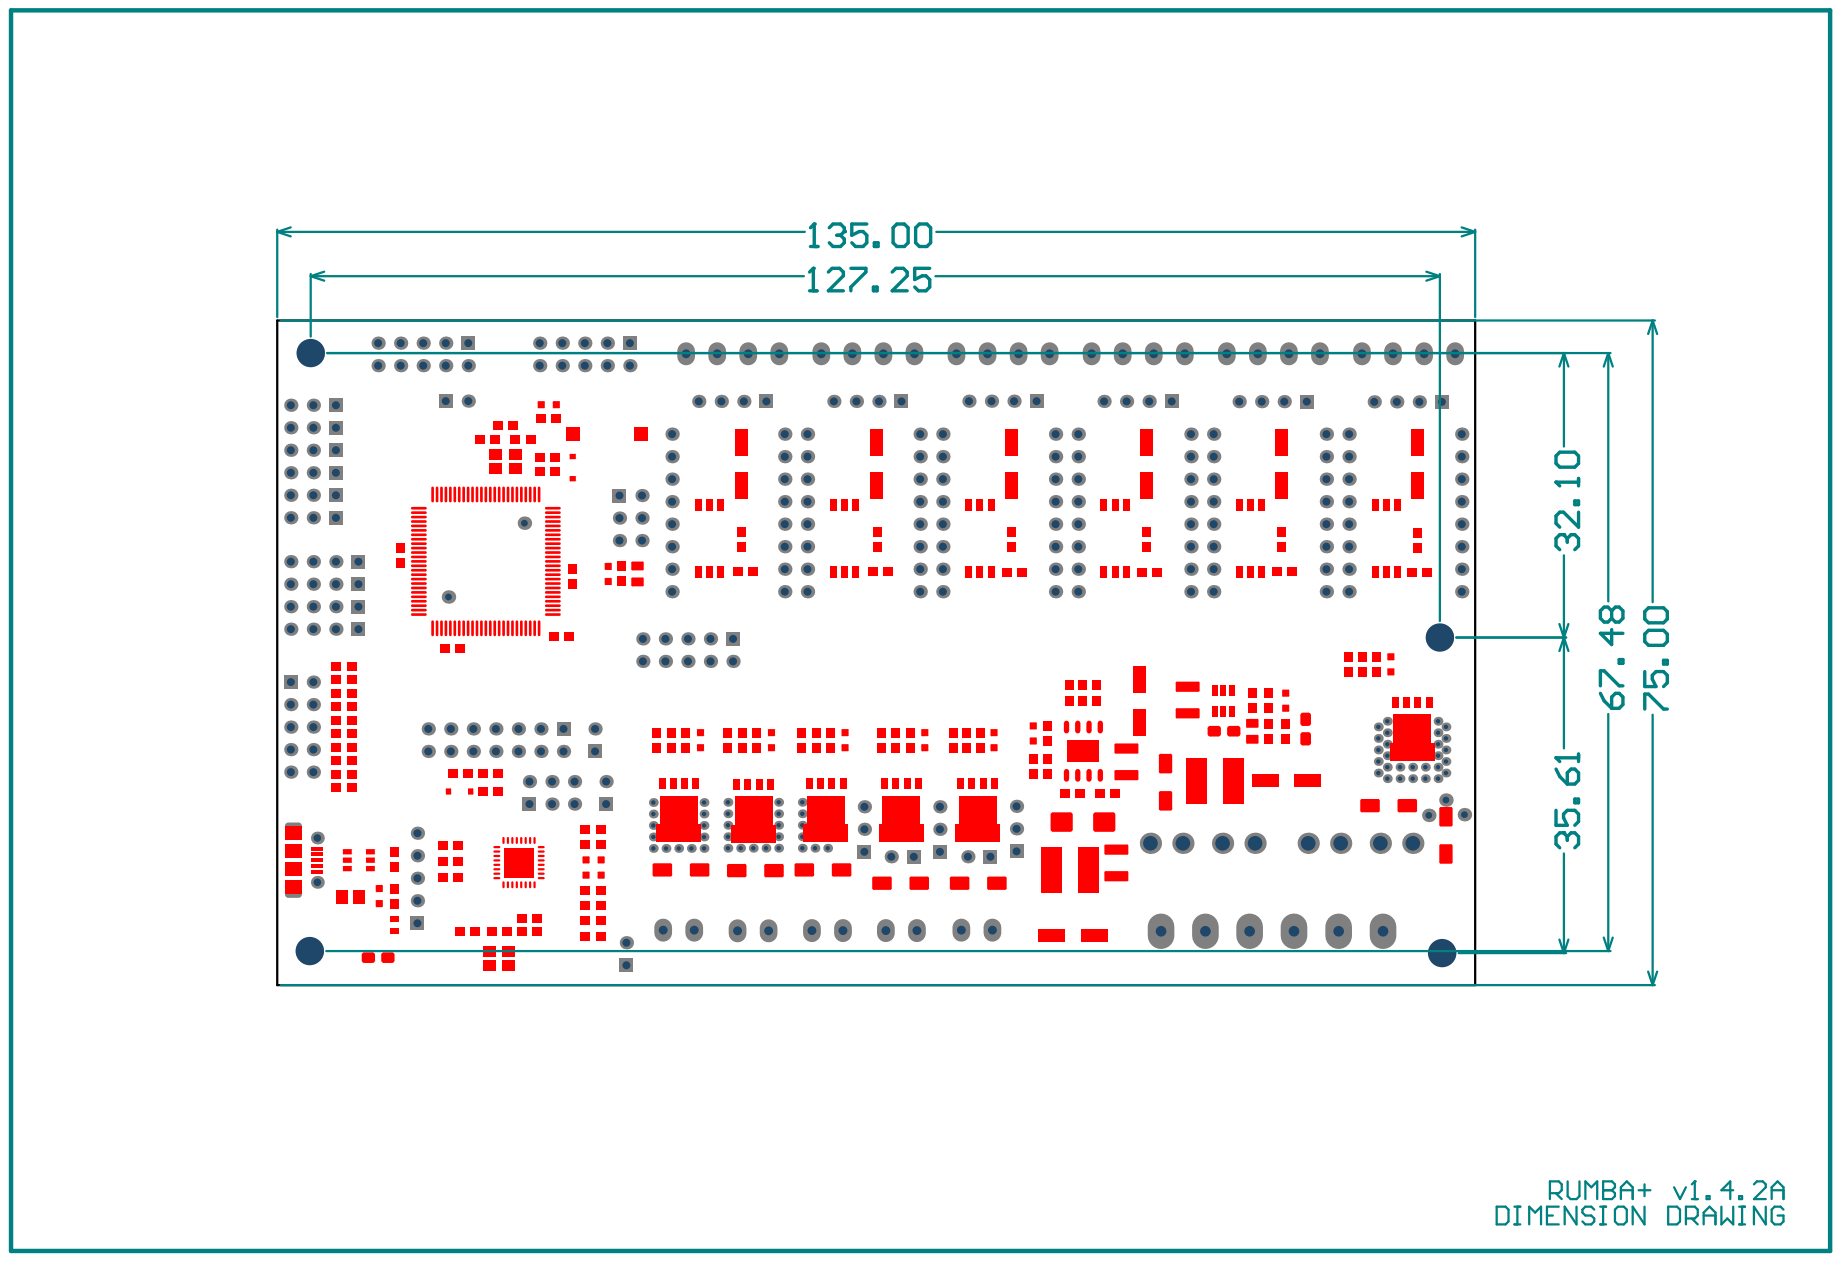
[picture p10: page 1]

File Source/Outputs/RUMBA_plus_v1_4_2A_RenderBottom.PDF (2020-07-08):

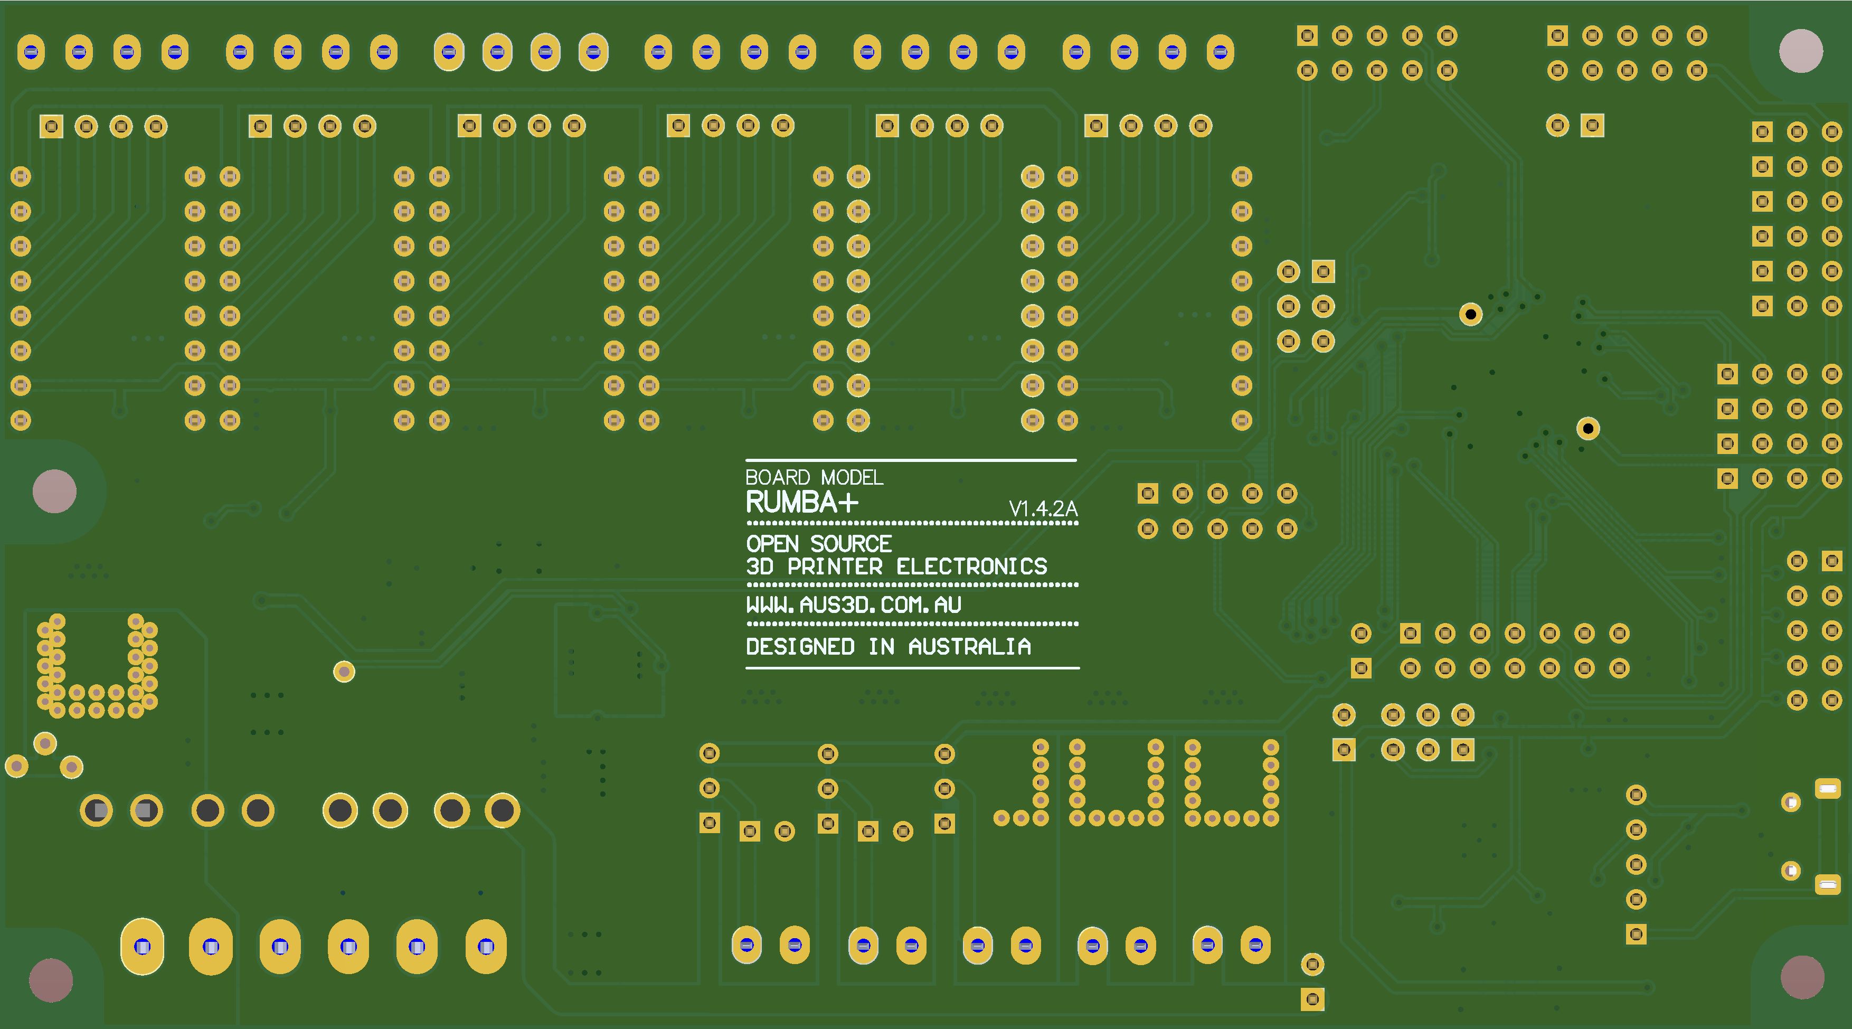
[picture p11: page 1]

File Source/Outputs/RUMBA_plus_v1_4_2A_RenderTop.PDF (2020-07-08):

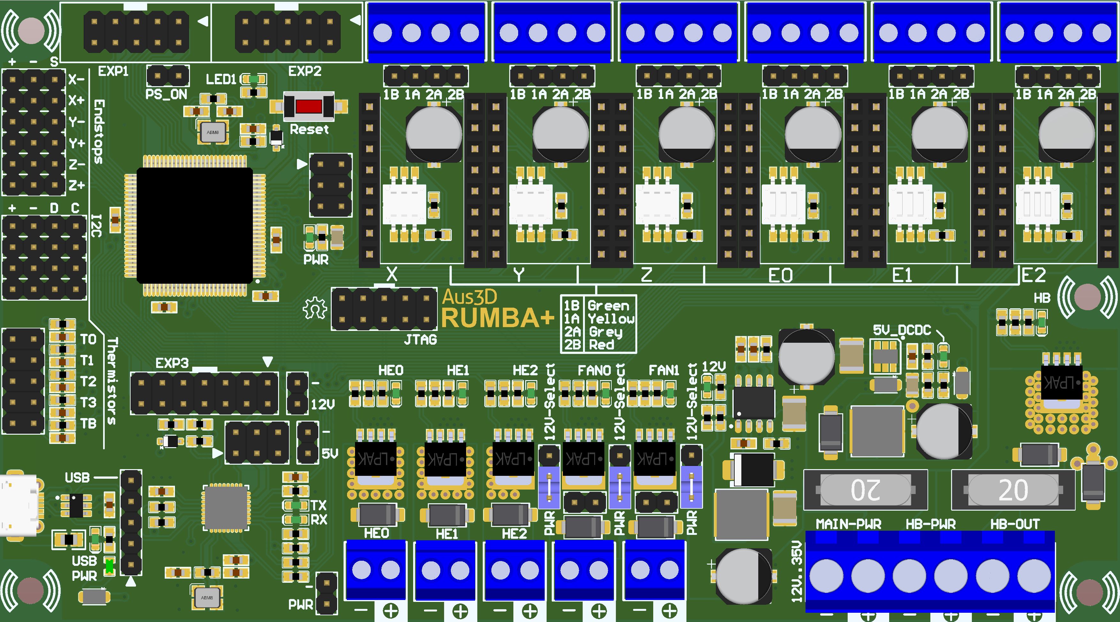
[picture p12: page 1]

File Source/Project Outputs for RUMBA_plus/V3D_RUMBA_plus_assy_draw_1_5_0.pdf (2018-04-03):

A

B

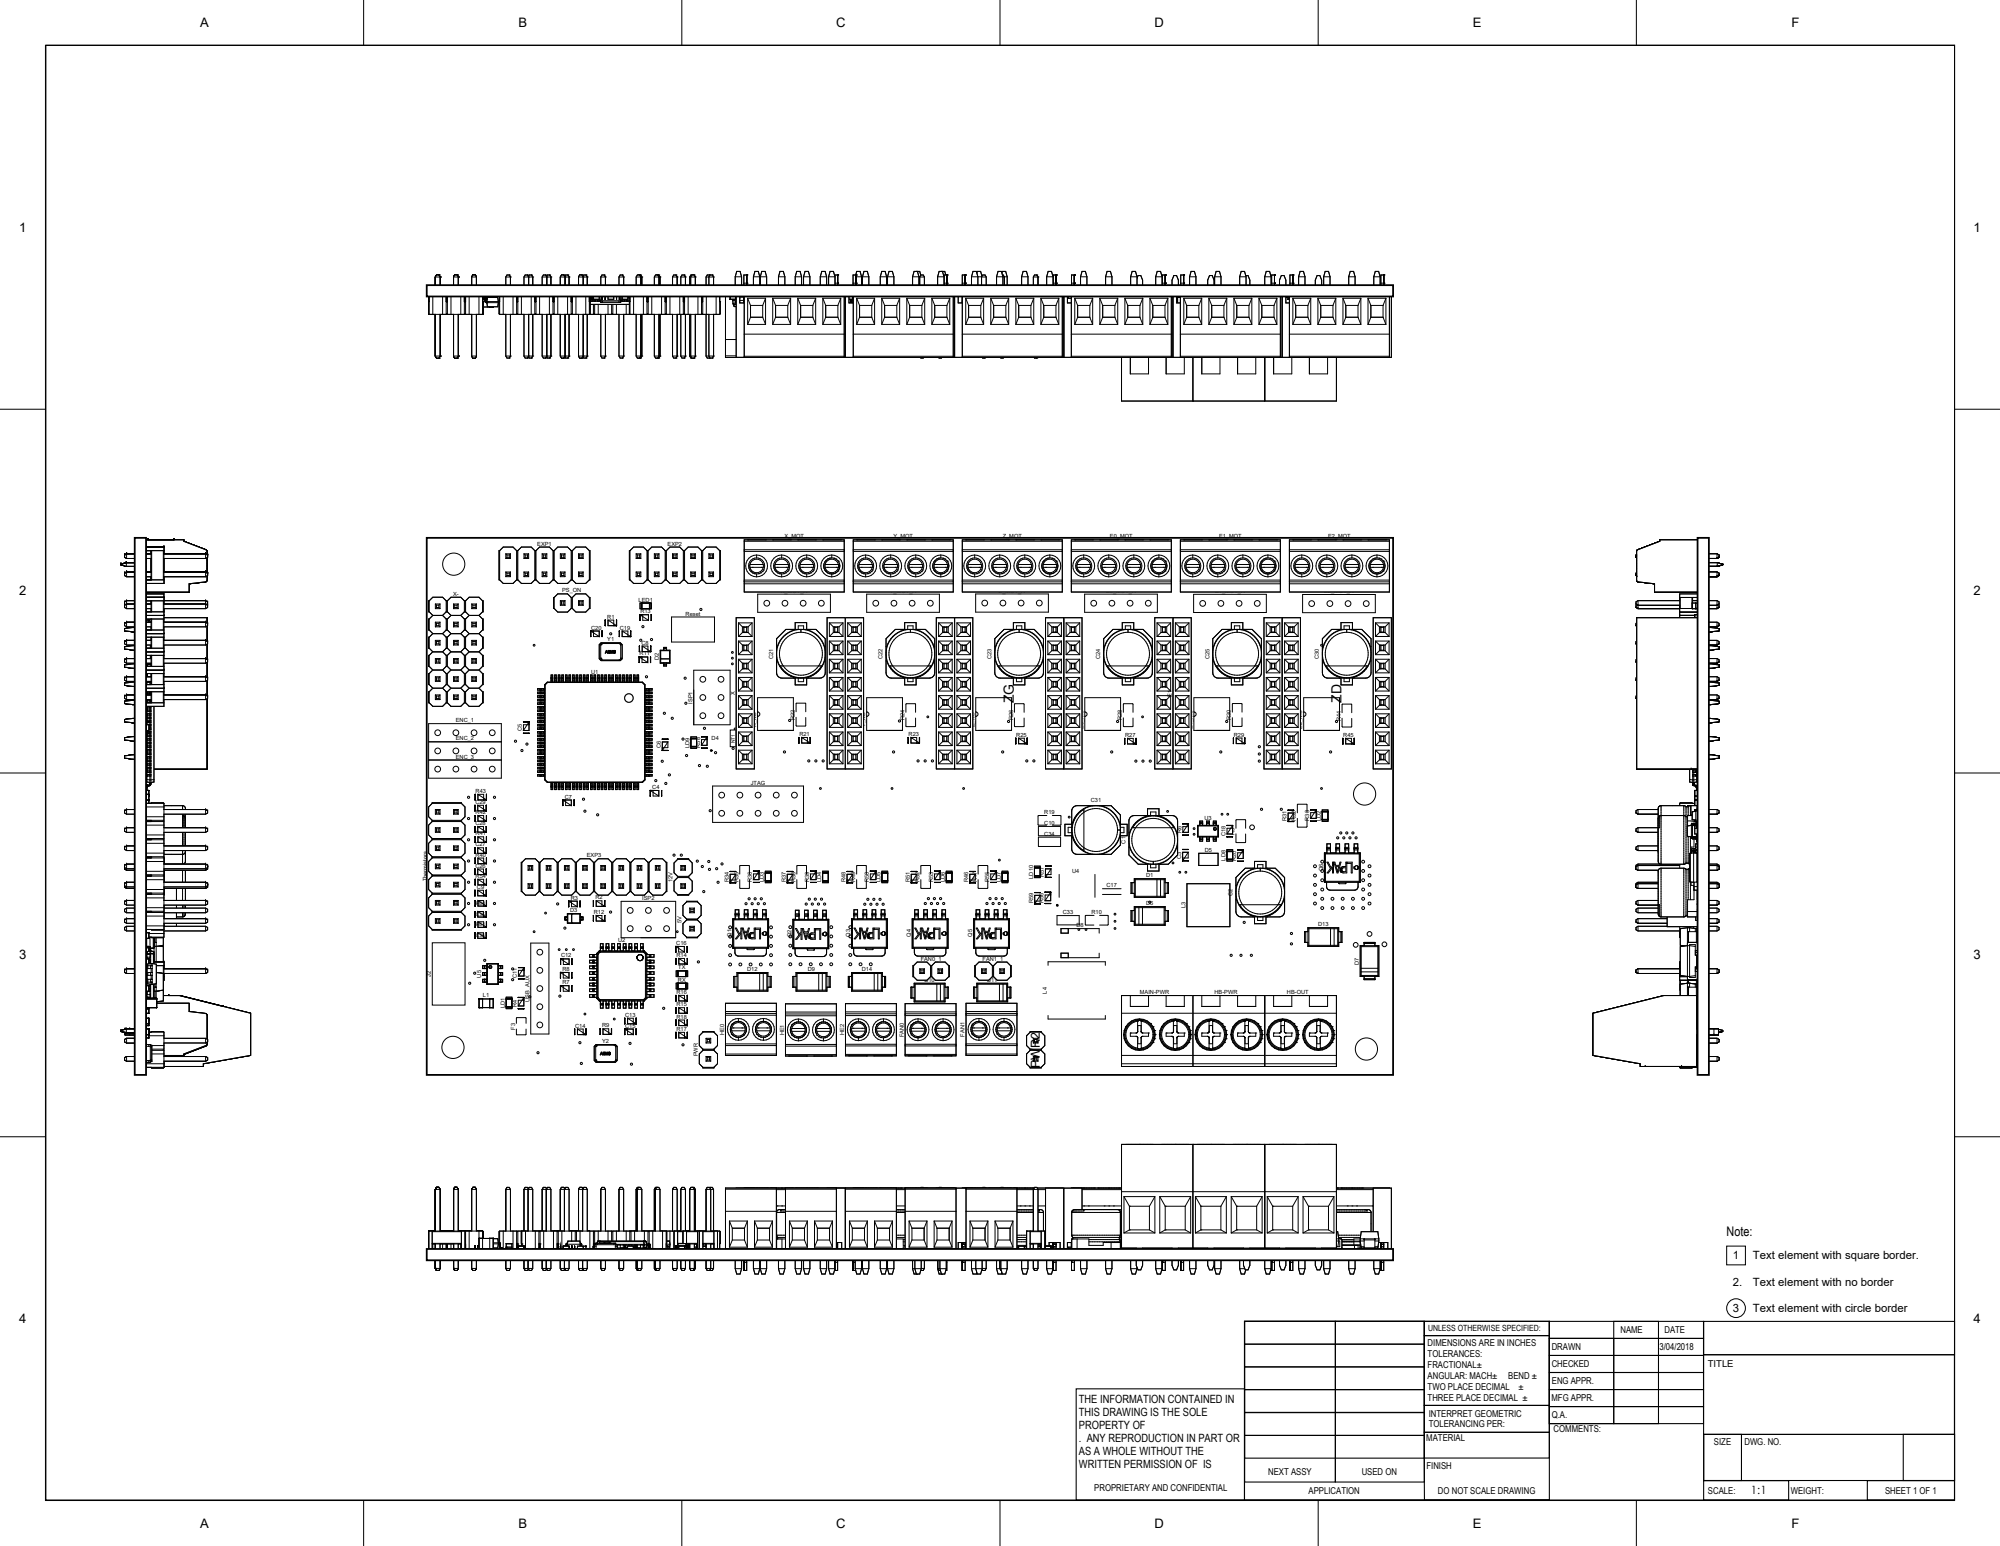
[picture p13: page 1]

1 Text element with square border.

2. Text element with no border

3 Text element with circle border

UNLESS OTHERWISE SPECIFIED:
DIMENSIONS ARE IN INCHES
TOLERANCES:
FRACTIONAL±
ANGULAR: MACH± BEND ±
TWO PLACE DECIMAL ±
THREE PLACE DECIMAL ±
INTERPRET GEOMETRIC
TOLERANCING PER:
MATERIAL

THE INFORMATION CONTAINED IN
THIS DRAWING IS THE SOLE
PROPERTY OF
. ANY REPRODUCTION IN PART OR
AS A WHOLE WITHOUT THE
WRITTEN PERMISSION OF IS

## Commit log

2018-01-04 Initial Volumic3D Changes
    Routing / functionality changes:
    -Removed fuses F1 and F2, VIN and VBED are routed on PCB
    -Removed HE2, FAN0 and FAN1 voltage select jumpers, fixed to VIN
    -Removed microstepping switches, MS lines fixed to 5V
    -Removed 5V diode, 5V_DCDC connected to 5V
    Removed BOM items:
    -ISP1 header
    -microUSB connector
    -USB aux header
    -JTAG header
    -I2C headers
    -PS_ON header
    -Reset button
    -Stepper pin headers
    [RUMBA_plus.SchDoc, RUMBA_plus_BOM_1_3_1.xlsx]
2018-01-17 Continued Volumic3D Changes
    - Remove 12V Regulator
    - Tidy board routing
    - Finalise BOM
    - Finalise Gerbers
    [RUMBA_plus.PrjPCB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]
2018-04-03 Volumic3D v1.5a
    Add two extra thermistors
    Rework EXP3 connector
    Remove 1 I2C Encoder connector
    Add PWR2 header
    Change screw terminals to part with rising cage clamp design
    [RUMBA_plus.PrjPCB, RUMBA_plus.SchDoc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]
2018-04-11 Change EXP3 from 7x2 to 8x2 in BOM
    [V3D_RUMBA_plus_BOM_1_5_0.xlsx]
2019-02-16 PCB fixes
    Improvements for manufacturing based on previous batches:
    - Increase clearance around cut-points for stepper MS lines (remove possibility of shorting to ground if solder paste is deposited)
    - Connect Y1 and Y2 casing to ground as recommended in datasheet (improve board EMC).
    PCB updated to v1.5b.
2019-02-16 1.5b PCB revision gerbers
2019-02-16 Tidy outputs
    [Assembly Testpoint Report for RUMBA_plus.csv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]
2019-02-16 Tidy output files
    [Assembly Testpoint Report for RUMBA_plus.csv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]
2019-05-25 Fix incorrect part numbers
    [RUMBA_plus_BOM_1_4_0.xlsx]
2019-05-25 Remove unused files
    [RUMBA_plus.PrjPCB]
2019-05-25 Reorganise v1.41 outputs
    Only difference with v1.41 is that 16u2 was changed from -AU to -MU package.
    Renaming output files for consistency.
    [RUMBA_plus_BOM_1_4_1.xlsx]
2019-05-25 Tidying
    Update schematic parts so that BOM can be generated automatically and correctly.
    Update .gitignore to ignore unneeded files.
    [RUMBA_plus.PrjPCB, RUMBA_plus.SchDoc]
2019-05-27 Schematic changes
    Bring in improvements from RUMBA32 development. Mostly changes to 5V and 12V regulator sections.
    - Replace dual diode D4 with two separate parts
    - Remove electrolytic cap C31 on VIN and replace with ceramic cap
    - Remove diode D1
    - Add ceramic caps to outputs of both regulators
    - Change inductor L4 from 47uH 2A to 4.7uH 4A, and change compensation network to suit new inductance
    - Add 4.7uF ceramic cap to 5V rail near 2560
    [RUMBA_plus.SchDoc]
2019-05-27 Update PCB
    Update with schematic changes
    TIdy silkscreen labels on aux power pins
2019-05-27 Generate outputs for v1.4.2A
    [RUMBA_plus_BOM_1_4_2A.xlsx, RUMBA_plus_pickplace_1_4_2A.csv]
2019-05-29 Add jumpers + note
    Add jumpers to schematic, drawing and BOM.
    Add note about removal of Kapton from DIP switches to drawing.
    [RUMBA_plus.SchDoc, RUMBA_plus_BOM_1_4_2A.xlsx]
2019-05-29 Rename outputs for consistency
    Easier to group outputs by version and consistent with other projects
    [RUMBA_plus_1_3_1_BOM.xlsx, RUMBA_plus_1_3_1_pickplace.csv, RUMBA_plus_1_4_0_BOM.xlsx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]
2019-05-29 Fix 5mm terminal in BOM
    Same part was on two lines in BOM, combine / fix in source and regenerate.
    [RUMBA_plus.SchDoc, RUMBA_plus_1_4_2A_BOM.xlsx]
2020-07-08 Tidy outputs
    Rename outputs and output folders for consistency.
    Update outjob settings for easier file generation in future.
    [RUMBA_plus.PrjPCB, RUMBA_plus_v1_3_1_BOM.xlsx, RUMBA_plus_v1_3_1_PickPlace.csv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]
2020-07-08 Add pinout and dimension drawings
    [RUMBA_plus.PrjPCB]
2020-07-08 Reorganise images, update README
    Add pinout and dimension images, add to readme, rename files, tidy.
    [RUMBA_plus_1_4_2A_BOM.xlsx, RUMBA_plus_v1_4_2A_BOM.xlsx]

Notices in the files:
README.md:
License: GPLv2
